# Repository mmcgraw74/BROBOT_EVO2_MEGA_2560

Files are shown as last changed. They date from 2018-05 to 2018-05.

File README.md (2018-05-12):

# BROBOT-EVO2-MEGA-2560

This project is a modification of the JJRobots EVO2 balancing robot:
https://github.com/jjrobots/B-ROBOT_EVO2

I wanted more I/O and program space - so replaced the Arduino Leonardo in the kit with an Arduino Mega 2560.

Since the Mega 2560 is over an inch longer - I used Meshmixer to cut the Stealth files and Simplify3d to stretch and merge the pieces to extend the width of the chassis to 130mm.  My efforts did not get both of the mounting holes in the rear bumper STL - I just drilled a hole manually. 

I had to modify the Leonardo program files for several things that are different in the Mega 2560:
- Mega i2c pins are outside the EVO2 shield - so I plugged two long header pins into the Mega i2c pins and plugged in the i2c CLK and DATA pins from the Gyro cable into the Mega.
- Mega Serial0 (console) is on pins 0 and 1, so I unsoldered the shield pins 0 and 1 out and moved the pins to the top of the board and jumpered the pins to Mega TX1 and RX1.
- I changed the servo code to use the SoftwareServo library. The Servo library conflicted with the Wire library. Then I changed the servo code to make library calls. If I was more proficient at Arduino timer code - I might have been able to not use the softwareservo library and initialize the Mega timers.
- I changed the PORT and bit from Leonardo to Mega 2560 to get the stepper motor code to work with the Mega.
- I merged my Touch OSC code changes which provide battery voltage and battery percentage plus PID values on the PID screen

This is still a work in progress:  the additional mass has not been factored into the default PIDs, so the Mega EVO2 is drivable in PRO mode, but not as stable as the Leonardo EVO2 yet.

All Arduino files are included, my stretched Stealth Remix EVO2 chassis STL files and my TOUCH OSC file - works with my iPHONE6s

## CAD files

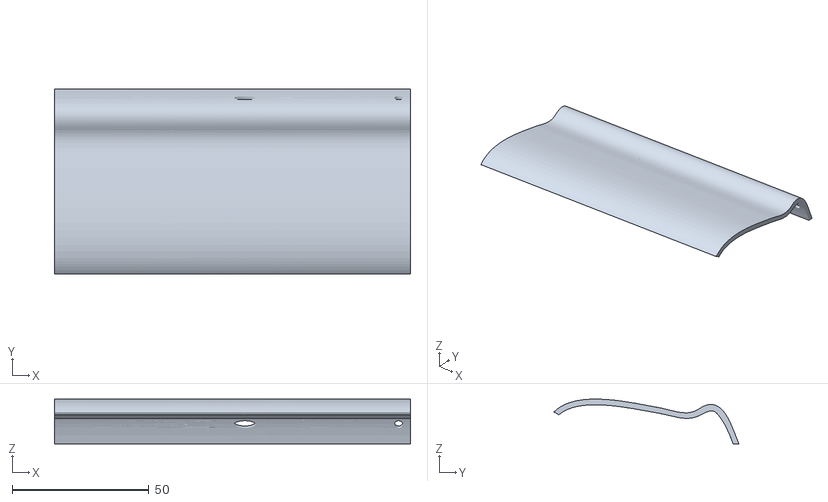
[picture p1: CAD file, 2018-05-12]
EVO2 Mega STL files/130mm front bumper_fixed.stl
130.0 x 67.5 x 16.4

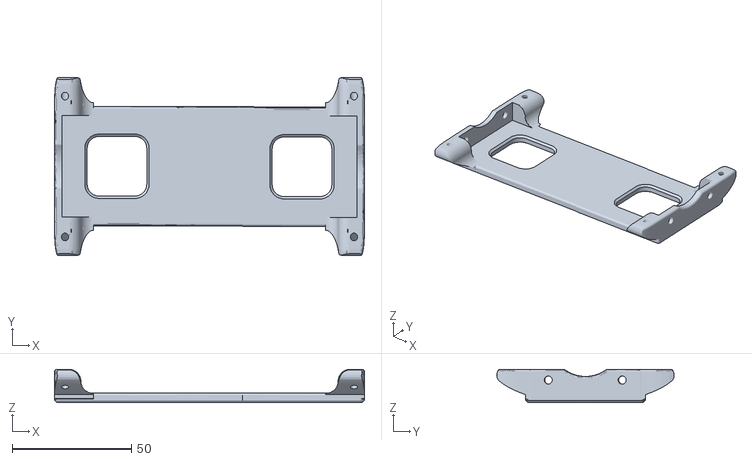
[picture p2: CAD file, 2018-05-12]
EVO2 Mega STL files/130mm motor extended_fixed.stl
130.0 x 74.4 x 14.0

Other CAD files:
EVO2 Mega STL files/130mm back bumper_fixed.stl

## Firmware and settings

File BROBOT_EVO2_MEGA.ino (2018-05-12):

// BROBOT EVO 2 by JJROBOTS
// SELF BALANCE ARDUINO ROBOT WITH STEPPER MOTORS CONTROLLED WITH YOUR SMARTPHONE
// JJROBOTS BROBOT KIT: (Arduino Mega + BROBOT ELECTRONIC BRAIN SHIELD + STEPPER MOTOR drivers)
// This code is prepared for new BROBOT shield  with ESP8266 Wifi module
// Author: JJROBOTS.COM
// Date: 02/09/2014
// Updated: 25/06/2017
// Modified: 10/05/2018 by Monty McGraw (Nikola-wan) for Arduino Mega
// Version: 2.82
// License: GPL v2
// Compiled and tested with Arduino 1.8.5. This modified version of code adds SoftwareServo (only Arduino standard libraries)
// Project URL: http://jjrobots.com/b-robot-evo-2-much-more-than-a-self-balancing-robot (Features,documentation,build instructions,how it works, SHOP,...)
// New updates:
//   - New default parameters specially tuned for BROBOT EVO 2 version (More agile, more stable...)
//   - New Move mode with position control (for externally programming the robot with a Blockly or pyhton programming interfaces)
//   - New telemtry packets send to TELEMETRY IP for monitoring Battery, Angle, ... (old battery packets for touch osc not working now)
//   - Default telemetry server is 192.168.4.2 (first client connected to the robot)
//  Get the free android app (jjrobots) from google play. For IOS users you need to use TouchOSC App + special template (info on jjrobots page)
//  Thanks to our users on the forum for the new ideas. Specially sasa999, KomX, ...

// The board needs at least 10-15 seconds with no motion (robot steady) at beginning to give good values... Robot move slightly when it´s ready!
// MPU6050 IMU connected via I2C bus. Angle estimation using complementary filter (fusion between gyro and accel)
// Angle calculations and control part is running at 100Hz

// The robot is OFF when the angle is high (robot is horizontal). When you start raising the robot it
// automatically switch ON and start a RAISE UP procedure.
// You could RAISE UP the robot also with the robot arm servo (Servo button on the interface)
// To switch OFF the robot you could manually put the robot down on the floor (horizontal)

// We use a standard PID controllers (Proportional, Integral derivative controller) for robot stability
// More info on the project page: How it works page at jjrobots.com
// We have a PI controller for speed control and a PD controller for stability (robot angle)
// The output of the control (motors speed) is integrated so it´s really an acceleration not an speed.

// We control the robot from a WIFI module using OSC standard UDP messages
// You need an OSC app to control de robot (Custom free JJRobots APP for android, and TouchOSC APP for IOS)
// Join the module Wifi Access Point (by default: JJROBOTS_XX) with your Smartphone/Tablet...
//   Wifi password: 87654321
// For TouchOSC users (IOS): Install the BROBOT layout into the OSC app (Touch OSC) and start play! (read the project page)
// OSC controls:
//    fader1: Throttle (0.0-1.0) OSC message: /1/fader1
//    fader2: Steering (0.0-1.0) OSC message: /1/fader2
//    push1: Move servo arm (and robot raiseup) OSC message /1/push1
//    if you enable the touchMessage on TouchOSC options, controls return to center automatically when you lift your fingers
//    PRO mode (PRO button). On PRO mode steering and throttle are more aggressive
//    PAGE2: PID adjustements [optional][dont touch if you dont know what you are doing...;-) ]

#include <Wire.h>
#include <SoftwareServo.h>
SoftwareServo myservo1,myservo2;  // create servo object to control two servos

// Uncomment this lines to connect to an external Wifi router (join an existing Wifi network)
//#define EXTERNAL_WIFI
//#define WIFI_SSID "YOUR_WIFI"
//#define WIFI_PASSWORD "YOUR_PASSWORD"
//#define WIFI_IP "192.168.1.101"  // Force ROBOT IP
//#define TELEMETRY "192.168.1.38" // Tlemetry server port 2223

#define TELEMETRY "192.168.4.2" // Default telemetry server (first client) port 2223

// NORMAL MODE PARAMETERS (MAXIMUN SETTINGS)
#define MAX_THROTTLE 550
#define MAX_STEERING 140
#define MAX_TARGET_ANGLE 14

// PRO MODE = MORE AGGRESSIVE (MAXIMUN SETTINGS)
#define MAX_THROTTLE_PRO 780   // Max recommended value: 860
#define MAX_STEERING_PRO 260   // Max recommended value: 280
#define MAX_TARGET_ANGLE_PRO 26   // Max recommended value: 32

// Default control terms for EVO 2
#define KP 0.32       
#define KD 0.050     
#define KP_THROTTLE 0.080 
#define KI_THROTTLE 0.1

float Kpu_old;
float Kdu_old;
float Kpt_old;
float Kit_old;

#define KP_POSITION 0.06  
#define KD_POSITION 0.45  
//#define KI_POSITION 0.02

// Control gains for raiseup (the raiseup movement requiere special control parameters)
#define KP_RAISEUP 0.1   
#define KD_RAISEUP 0.16   
#define KP_THROTTLE_RAISEUP 0   // No speed control on raiseup
#define KI_THROTTLE_RAISEUP 0.0

#define MAX_CONTROL_OUTPUT 500
#define ITERM_MAX_ERROR 30   // Iterm windup constants for PI control 
#define ITERM_MAX 10000

#define ANGLE_OFFSET 0.0  // Offset angle for balance (to compensate robot own weight distribution)

// Servo definitions
#define SERVO_AUX_NEUTRO 90  // Servo neutral position in degrees
#define SERVO_MIN_PULSEWIDTH 0
#define SERVO_MAX_PULSEWIDTH 180

#define SERVO2_NEUTRO 90
#define SERVO2_RANGE 180


// Telemetry
#define TELEMETRY_BATTERY 1
#define TELEMETRY_ANGLE 1
//#define TELEMETRY_DEBUG 1  // Dont use TELEMETRY_ANGLE and TELEMETRY_DEBUG at the same time!

#define ZERO_SPEED 65535
#define MAX_ACCEL 14      // Maximun motor acceleration (MAX RECOMMENDED VALUE: 20) (default:14)

#define MICROSTEPPING 16   // 8 or 16 for 1/8 or 1/16 driver microstepping (default:16)

#define DEBUG 1   // 0 = No debug info (default) DEBUG 1 for console output

// AUX definitions
#define CLR(x,y) (x&=(~(1<<y)))
#define SET(x,y) (x|=(1<<y))
#define RAD2GRAD 57.2957795
#define GRAD2RAD 0.01745329251994329576923690768489

String MAC;  // MAC address of Wifi module
String tempstring;

unsigned int testVal = 0;
uint8_t cascade_control_loop_counter = 0;
uint8_t loop_counter;       // To generate a medium loop 40Hz
uint8_t slow_loop_counter;  // slow loop 2Hz
uint8_t sendBattery_counter; // To send battery status
int16_t BatteryValue;
static char outstr[4];
float BatteryFloat;
float BatteryReal;

long timer_old;
long timer_value;
float debugVariable;
float dt;

// Angle of the robot (used for stability control)
float angle_adjusted;
float angle_adjusted_Old;
float angle_adjusted_filtered = 0.0;

// Default control values from constant definitions
float Kp = KP;
float Kd = KD;
float Kp_thr = KP_THROTTLE;
float Ki_thr = KI_THROTTLE;
float Kp_user = KP;
float Kd_user = KD;
float Kp_thr_user = KP_THROTTLE;
float Ki_thr_user = KI_THROTTLE;
float Kp_position = KP_POSITION;
float Kd_position = KD_POSITION;
bool newControlParameters = false;
bool modifing_control_parameters = false;
int16_t position_error_sum_M1;
int16_t position_error_sum_M2;
float PID_errorSum;
float PID_errorOld = 0;
float PID_errorOld2 = 0;
float setPointOld = 0;
float target_angle;
int16_t throttle;
float steering;
float max_throttle = MAX_THROTTLE;
float max_steering = MAX_STEERING;
float max_target_angle = MAX_TARGET_ANGLE;
float control_output;
float angle_offset = ANGLE_OFFSET;

boolean positionControlMode = false;
uint8_t mode;  // mode = 0 Normal mode, mode = 1 Pro mode (More agressive)

int16_t motor1;
int16_t motor2;

// position control
volatile int32_t steps1;
volatile int32_t steps2;
int32_t target_steps1;
int32_t target_steps2;
int16_t motor1_control;
int16_t motor2_control;

int16_t speed_M1, speed_M2;        // Actual speed of motors
int8_t  dir_M1, dir_M2;            // Actual direction of steppers motors
int16_t actual_robot_speed;        // overall robot speed (measured from steppers speed)
int16_t actual_robot_speed_Old;
float estimated_speed_filtered;    // Estimated robot speed

// OSC output variables
uint8_t OSCpage;
uint8_t OSCnewMessage;
float OSCfader[4];
float OSCxy1_x;
float OSCxy1_y;
float OSCxy2_x;
float OSCxy2_y;
uint8_t OSCpush[4];
uint8_t OSCtoggle[4];
uint8_t OSCmove_mode;
int16_t OSCmove_speed;
int16_t OSCmove_steps1;
int16_t OSCmove_steps2;


// INITIALIZATION
void setup()
{
  // STEPPER PINS ON JJROBOTS BROBOT BRAIN BOARD
  pinMode(4, OUTPUT); // ENABLE MOTORS
  pinMode(7, OUTPUT); // STEP MOTOR 1 PORTE,6
  pinMode(8, OUTPUT); // DIR MOTOR 1  PORTB,4
  pinMode(12, OUTPUT); // STEP MOTOR 2 PORTD,6
  pinMode(5, OUTPUT); // DIR MOTOR 2  PORTC,6
  digitalWrite(4, HIGH);  // Disable motors
  /*
  pinMode(10, OUTPUT);  // Servo1 (arm)
  pinMode(13, OUTPUT);  // Servo2
  */
  Serial.begin(115200); // Serial output to console
  
  Serial1.begin(115200);
  OSC_init();

  // Initialize I2C bus (MPU6050 is connected via I2C)
  Wire.begin();

#if DEBUG > 0
  delay(9000);
#else
  delay(1000);
#endif
  Serial.println("JJROBOTS");
  delay(200);
  Serial.println("Don't move for 10 sec...");
  MPU6050_setup();  // setup MPU6050 IMU
  delay(500);

  // With the new ESP8266 WIFI MODULE WE NEED TO MAKE AN INITIALIZATION PROCESS
  Serial.println("WIFI init");
  Serial1.flush();
  Serial1.print("+++");  // To ensure we exit the transparent transmision mode
  delay(100);
  ESPsendCommand("AT", "OK", 1);
  ESPsendCommand("AT+RST", "OK", 2); // ESP Wifi module RESET
  ESPwait("ready", 6);
  ESPsendCommand("AT+GMR", "OK", 5);

#ifdef EXTERNAL_WIFI
  ESPsendCommand("AT+CWQAP", "OK", 3);
  ESPsendCommand("AT+CWMODE=1", "OK", 3);
  //String auxCommand = (String)"AT+CWJAP="+WIFI_SSID+","+WIFI_PASSWORD;
  char auxCommand[90] = "AT+CWJAP=\"";
  strcat(auxCommand, WIFI_SSID);
  strcat(auxCommand, "\",\"");
  strcat(auxCommand, WIFI_PASSWORD);
  strcat(auxCommand, "\"");
  ESPsendCommand(auxCommand, "OK", 14);
#ifdef WIFI_IP
  strcpy(auxCommand, "AT+CIPSTA=\"");
  strcat(auxCommand, WIFI_IP);
  strcat(auxCommand, "\"");
  ESPsendCommand(auxCommand, "OK", 4);
#endif
  ESPsendCommand("AT+CIPSTA?", "OK", 4);
#else  // Deafault : we generate a wifi network
  Serial1.println("AT+CIPSTAMAC?");
  ESPgetMac();
  //Serial.print("MAC:");
  //Serial.println(MAC);
  delay(200);
  ESPsendCommand("AT+CWQAP", "OK", 3);
  ESPsendCommand("AT+CWMODE=2", "OK", 3); // Soft AP mode
  // Generate Soft AP. SSID=JJROBOTS, PASS=87654321
  char *cmd =  "AT+CWSAP=\"JJROBOTS_XX\",\"87654321\",5,3";
  // Update XX characters with MAC address (last 2 characters)
  cmd[19] = MAC[10];
  cmd[20] = MAC[11];
  ESPsendCommand(cmd, "OK", 6);
#endif
  // Start UDP SERVER on port 2222, telemetry port 2223
  Serial.println("Start UDP server");
  ESPsendCommand("AT+CIPMUX=0", "OK", 3);  // Single connection mode
  ESPsendCommand("AT+CIPMODE=1", "OK", 3); // Transparent mode
  char Telemetry[80];
  strcpy(Telemetry, "AT+CIPSTART=\"UDP\",\"");
  strcat(Telemetry, TELEMETRY);
  strcat(Telemetry, "\",2223,2222,0");
  ESPsendCommand(Telemetry, "OK", 3); 

  // Calibrate gyros
  MPU6050_calibrate();

  ESPsendCommand("AT+CIPSEND", ">", 2); // Start transmission (transparent mode)

  // Init servos
  Serial.println("Servo init");
  BROBOT_initServo();

  myservo1.attach(10);
  myservo2.attach(13);
  myservo1.write(SERVO_AUX_NEUTRO);
  myservo2.write(SERVO_AUX_NEUTRO);
  SoftwareServo::refresh();

  // STEPPER MOTORS INITIALIZATION
  Serial.println("Steppers init");
  //MOTOR1 => TIMER1
  TCCR1A = 0;                       // Timer1 CTC mode 4, OCxA,B outputs disconnected
  TCCR1B = (1 << WGM12) | (1 << CS11); // Prescaler=8, => 2Mhz
  OCR1A = ZERO_SPEED;               // Motor stopped
  dir_M1 = 0;
  TCNT1 = 0;

  // MOTOR2 => TIMER3
  TCCR3A = 0;                       // Timer3 CTC mode 4, OCxA,B outputs disconnected
  TCCR3B = (1 << WGM32) | (1 << CS31); // Prescaler=8, => 2Mhz
  OCR3A = ZERO_SPEED;   // Motor stopped
  dir_M2 = 0;
  TCNT3 = 0;
  delay(200);

  // Enable stepper drivers and TIMER interrupts
  digitalWrite(4, LOW);   // Enable stepper drivers
  // Enable TIMERs interrupts
  TIMSK1 |= (1 << OCIE1A); // Enable Timer1 interrupt
  TIMSK3 |= (1 << OCIE1A); // Enable Timer1 interrupt
  
  
  // Little motor vibration and servo move to indicate that robot is ready
  for (uint8_t k = 0; k < 5; k++)
  {
    /*setMotorSpeedM1(5);
    setMotorSpeedM2(5);
    */
    myservo1.write(SERVO_AUX_NEUTRO + 10);
    myservo2.write(SERVO2_NEUTRO + 10);
    SoftwareServo::refresh();
    delay(200);
    /* setMotorSpeedM1(-5);
    setMotorSpeedM2(-5);
    */
    
    myservo1.write(SERVO_AUX_NEUTRO - 10);
    myservo2.write(SERVO2_NEUTRO - 10);
    SoftwareServo::refresh();
    delay(200);
  }
  myservo1.write(SERVO_AUX_NEUTRO);
  myservo2.write(SERVO2_NEUTRO);
  SoftwareServo::refresh();

 #if TELEMETRY_BATTERY==1
  BatteryValue = BROBOT_readBattery(true);
  Serial.print("BATT:");
  Serial.println(BatteryValue);
#endif
  Serial.println("BROBOT by JJROBOTS v2.82");
  Serial.println("Start...");
  timer_old = micros();
}


// MAIN LOOP
void loop()
{
  OSC_MsgRead();  // Read UDP OSC messages
  if (OSCnewMessage)
  {
    OSCnewMessage = 0;
    if (OSCpage == 1)   // Get commands from user (PAGE1 are user commands: throttle, steering...)
    {
      if (modifing_control_parameters)  // We came from the settings screen
      {
        OSCfader[0] = 0.5; // default neutral values
        OSCfader[1] = 0.5;
        OSCtoggle[0] = 0;  // Normal mode
        mode = 0;
        modifing_control_parameters = false;
      }

      if (OSCmove_mode)
      {
        //Serial.print("M ");
        //Serial.print(OSCmove_speed);
        //Serial.print(" ");
        //Serial.print(OSCmove_steps1);
        //Serial.print(",");
        //Serial.println(OSCmove_steps2);
        positionControlMode = true;
        OSCmove_mode = false;
        target_steps1 = steps1 + OSCmove_steps1;
        target_steps2 = steps2 + OSCmove_steps2;
      }
      else
      {
        positionControlMode = false;
        throttle = (OSCfader[0] - 0.5) * max_throttle;
        // We add some exponential on steering to smooth the center band
        steering = OSCfader[1] - 0.5;
        if (steering > 0)
          steering = (steering * steering + 0.5 * steering) * max_steering;
        else
          steering = (-steering * steering + 0.5 * steering) * max_steering;
      }

      if ((mode == 0) && (OSCtoggle[0]))
      {
        // Change to PRO mode
        max_throttle = MAX_THROTTLE_PRO;
        max_steering = MAX_STEERING_PRO;
        max_target_angle = MAX_TARGET_ANGLE_PRO;
        mode = 1;
      }
      if ((mode == 1) && (OSCtoggle[0] == 0))
      {
        // Change to NORMAL mode
        max_throttle = MAX_THROTTLE;
        max_steering = MAX_STEERING;
        max_target_angle = MAX_TARGET_ANGLE;
        mode = 0;
      }
    }
    else if (OSCpage == 2) { // OSC page 2
      // Check for new user control parameters
      readControlParameters();
    }
#if DEBUG==1
    Serial.print(throttle);
    Serial.print(" ");
    Serial.println(steering);
#endif
  } // End new OSC message

  timer_value = micros();

  // New IMU data?
  if (MPU6050_newData())
  {
    MPU6050_read_3axis();
    loop_counter++;
    slow_loop_counter++;
    dt = (timer_value - timer_old) * 0.000001; // dt in seconds
    timer_old = timer_value;

    angle_adjusted_Old = angle_adjusted;
    // Get new orientation angle from IMU (MPU6050)
    float MPU_sensor_angle = MPU6050_getAngle(dt);
    angle_adjusted = MPU_sensor_angle + angle_offset;
    if ((MPU_sensor_angle>-15)&&(MPU_sensor_angle<15))
      angle_adjusted_filtered = angle_adjusted_filtered*0.99 + MPU_sensor_angle*0.01;
      
#if DEBUG==1
    Serial.print(dt);
    Serial.print(" ");
    Serial.print(angle_offset);
    Serial.print(" ");
    Serial.print(angle_adjusted);
    Serial.print(",");
    Serial.println(angle_adjusted_filtered);
#endif
    //Serial.print("\t");

    // We calculate the estimated robot speed:
    // Estimated_Speed = angular_velocity_of_stepper_motors(combined) - angular_velocity_of_robot(angle measured by IMU)
    actual_robot_speed = (speed_M1 + speed_M2) / 2; // Positive: forward  

    int16_t angular_velocity = (angle_adjusted - angle_adjusted_Old) * 25.0; // 25 is an empirical extracted factor to adjust for real units
    int16_t estimated_speed = -actual_robot_speed + angular_velocity;
    estimated_speed_filtered = estimated_speed_filtered * 0.9 + (float)estimated_speed * 0.1; // low pass filter on estimated speed

#if DEBUG==2
    Serial.print(angle_adjusted);
    Serial.print(" ");
    Serial.println(estimated_speed_filtered);
#endif

    if (positionControlMode)
    {
      // POSITION CONTROL. INPUT: Target steps for each motor. Output: motors speed
      motor1_control = positionPDControl(steps1, target_steps1, Kp_position, Kd_position, speed_M1);
      motor2_control = positionPDControl(steps2, target_steps2, Kp_position, Kd_position, speed_M2);

      // Convert from motor position control to throttle / steering commands
      throttle = (motor1_control + motor2_control) / 2;
      throttle = constrain(throttle, -190, 190);
      steering = motor2_control - motor1_control;
      steering = constrain(steering, -50, 50);
    }

    // ROBOT SPEED CONTROL: This is a PI controller.
    //    input:user throttle(robot speed), variable: estimated robot speed, output: target robot angle to get the desired speed
    target_angle = speedPIControl(dt, estimated_speed_filtered, throttle, Kp_thr, Ki_thr);
    target_angle = constrain(target_angle, -max_target_angle, max_target_angle); // limited output
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

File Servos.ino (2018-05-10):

// BROBOT EVO 2 by JJROBOTS
// SELF BALANCE ARDUINO ROBOT WITH STEPPER MOTORS
// License: GPL v2
// Servo and aux functions

//#include "Arduino.h"

/* Default servo definitions  commented out by MCM - we are using Servo library
#define SERVO1_AUX_NEUTRO 1500  // Servo neutral position
#define SERVO1_MIN_PULSEWIDTH 700
#define SERVO1_MAX_PULSEWIDTH 2300
#define SERVO2_AUX_NEUTRO 1500  // Servo neutral position
#define SERVO2_MIN_PULSEWIDTH 700
#define SERVO2_MAX_PULSEWIDTH 2300
*/

#define BATT_VOLT_FACTOR 8

int battery;

// Init servo on T4 timer. Output OC4B (Leonardo Pin10)
// We configure the Timer4 for 11 bits PWM (enhacend precision) and 16.3ms period (OK for most servos)
// Resolution: 8us per step (this is OK for servos, around 175 steps for typical servo)

/*
void BROBOT_initServo()
{
int temp;

  // Initialize Timer4 as Fast PWM
  TCCR4A = (1<<PWM4A)|(1<<PWM4B);
  TCCR4B = 0;
  TCCR4C = (1<<PWM4D);
  TCCR4D = 0;
  TCCR4E = (1<<ENHC4); // Enhanced -> 11 bits

  temp = 1500>>3;
  TC4H = temp >> 8;
  OCR4B = temp & 0xff;

  // Reset timer
  TC4H = 0;
  TCNT4 = 0;

  // Set TOP to 1023 (10 bit timer)
  TC4H = 3;
  OCR4C = 0xFF;

  // OC4A = PC7 (Pin13)  OC4B = PB6 (Pin10)   OC4D = PD7 (Pin6)
  // Set pins as outputs
  DDRB |= (1 << 6);  // OC4B = PB6 (Pin10 on Leonardo board)
  DDRC |= (1 << 7);  // OC4A = PC7 (Pin13 on Leonardo board)
  DDRD |= (1 << 7);  // OC4D = PD7 (Pin6 on Leonardo board)

  //Enable OC4A and OC4B and OCR4D output
  TCCR4A |= (1<<COM4B1)|(1<<COM4A1); 
  TCCR4C |= (1<<COM4D1);
  // set prescaler to 256 and enable timer    16Mhz/256/1024 = 61Hz (16.3ms)
  TCCR4B = (1 << CS43)|(1 << CS40);
}

void BROBOT_moveServo1(int pwm)
{
  pwm = constrain(pwm,SERVO1_MIN_PULSEWIDTH,SERVO1_MAX_PULSEWIDTH)>>3;  // Check max values and Resolution: 8us
  // 11 bits => 3 MSB bits on TC4H, LSB bits on OCR4B
  TC4H = pwm>>8;
  OCR4B = pwm & 0xFF;
}

void BROBOT_moveServo2(int pwm)
{
  pwm = constrain(pwm,SERVO2_MIN_PULSEWIDTH,SERVO2_MAX_PULSEWIDTH)>>3;  // Check max values and Resolution: 8us
  // 11 bits => 3 MSB bits on TC4H, LSB bits on OCR4B
  TC4H = pwm>>8;
  OCR4A = pwm & 0xFF;  // 2.0 or 2.3  boards servo2 output
  OCR4D = pwm & 0xFF;  // 2.1 or 2.4  boards servo2 output
}
*/

// output : Battery voltage*10 (aprox) and noise filtered
int BROBOT_readBattery(bool first_time)
{
  if (first_time)
	battery = analogRead(5)/BATT_VOLT_FACTOR;
  else
    battery = (battery*9 + (analogRead(5)/BATT_VOLT_FACTOR))/10;
  return battery;
}

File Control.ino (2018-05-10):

// BROBOT EVO 2 by JJROBOTS
// SELF BALANCE ARDUINO ROBOT WITH STEPPER MOTORS
// License: GPL v2
// Control functions (PID controls, Steppers control...)

// PD controller implementation(Proportional, derivative). DT in seconds
float stabilityPDControl(float DT, float input, float setPoint,  float Kp, float Kd)
{
  float error;
  float output;

  error = setPoint - input;

  // Kd is implemented in two parts
  //    The biggest one using only the input (sensor) part not the SetPoint input-input(t-1).
  //    And the second using the setpoint to make it a bit more agressive   setPoint-setPoint(t-1)
  float Kd_setPoint = constrain((setPoint - setPointOld), -8, 8); // We limit the input part...
  output = Kp * error + (Kd * Kd_setPoint - Kd * (input - PID_errorOld)) / DT;
  //Serial.print(Kd*(error-PID_errorOld));Serial.print("\t");
  //PID_errorOld2 = PID_errorOld;
  PID_errorOld = input;  // error for Kd is only the input component
  setPointOld = setPoint;
  return (output);
}


// PI controller implementation (Proportional, integral). DT in seconds
float speedPIControl(float DT, int16_t input, int16_t setPoint,  float Kp, float Ki)
{
  int16_t error;
  float output;

  error = setPoint - input;
  PID_errorSum += constrain(error, -ITERM_MAX_ERROR, ITERM_MAX_ERROR);
  PID_errorSum = constrain(PID_errorSum, -ITERM_MAX, ITERM_MAX);

  //Serial.println(PID_errorSum);

  output = Kp * error + Ki * PID_errorSum * DT; // DT is in miliseconds...
  return (output);
}


float positionPDControl(long actualPos, long setPointPos, float Kpp, float Kdp, int16_t speedM)
{
  float output;
  float P;

  P = constrain(Kpp * float(setPointPos - actualPos), -115, 115); // Limit command
  output = P + Kdp * float(speedM);
  return (output);
}

// TIMER 1 : STEPPER MOTOR1 SPEED CONTROL
ISR(TIMER1_COMPA_vect)
{
  if (dir_M1 == 0) // If we are not moving we dont generate a pulse
    return;
  // We generate 1us STEP pulse
  SET(PORTH, 4); // STEP MOTOR 1
  //delay_1us();
  if (dir_M1 > 0)
    steps1--;
  else
    steps1++;
  CLR(PORTH, 4);
}
// TIMER 3 : STEPPER MOTOR2 SPEED CONTROL
ISR(TIMER3_COMPA_vect)
{
  if (dir_M2 == 0) // If we are not moving we dont generate a pulse
    return;
  // We generate 1us STEP pulse
  SET(PORTB, 6); // STEP MOTOR 2
  //delay_1us();
  if (dir_M2 > 0)
    steps2--;
  else
    steps2++;
  CLR(PORTB, 6);
}


// Set speed of Stepper Motor1
// tspeed could be positive or negative (reverse)
void setMotorSpeedM1(int16_t tspeed)
{
  long timer_period;
  int16_t speed;

  // Limit max speed?

  // WE LIMIT MAX ACCELERATION of the motors
  if ((speed_M1 - tspeed) > MAX_ACCEL)
    speed_M1 -= MAX_ACCEL;
  else if ((speed_M1 - tspeed) < -MAX_ACCEL)
    speed_M1 += MAX_ACCEL;
  else
    speed_M1 = tspeed;

#if MICROSTEPPING==16
  speed = speed_M1 * 50; // Adjust factor from control output speed to real motor speed in steps/second
#else
  speed = speed_M1 * 25; // 1/8 Microstepping
#endif

  if (speed == 0)
  {
    timer_period = ZERO_SPEED;
    dir_M1 = 0;
  }
  else if (speed > 0)
  {
    timer_period = 2000000 / speed; // 2Mhz timer
    dir_M1 = 1;
    SET(PORTH, 5); // DIR Motor 1 (Forward)
  }
  else
  {
    timer_period = 2000000 / -speed;
    dir_M1 = -1;
    CLR(PORTH, 5); // Dir Motor 1
  }
  if (timer_period > 65535)   // Check for minimun speed (maximun period without overflow)
    timer_period = ZERO_SPEED;

  OCR1A = timer_period;
  // Check  if we need to reset the timer...
  if (TCNT1 > OCR1A)
    TCNT1 = 0;
}

// Set speed of Stepper Motor2
// tspeed could be positive or negative (reverse)
void setMotorSpeedM2(int16_t tspeed)
{
  long timer_period;
  int16_t speed;

  // Limit max speed?

  // WE LIMIT MAX ACCELERATION of the motors
  if ((speed_M2 - tspeed) > MAX_ACCEL)
    speed_M2 -= MAX_ACCEL;
  else if ((speed_M2 - tspeed) < -MAX_ACCEL)
    speed_M2 += MAX_ACCEL;
  else
    speed_M2 = tspeed;

#if MICROSTEPPING==16
  speed = speed_M2 * 50; // Adjust factor from control output speed to real motor speed in steps/second
#else
  speed = speed_M2 * 25; // 1/8 Microstepping
#endif

  if (speed == 0)
  {
    timer_period = ZERO_SPEED;
    dir_M2 = 0;
  }
  else if (speed > 0)
  {
    timer_period = 2000000 / speed; // 2Mhz timer
    dir_M2 = 1;
    CLR(PORTE, 3);   // Dir Motor2 (Forward)
  }
  else
  {
    timer_period = 2000000 / -speed;
    dir_M2 = -1;
    SET(PORTE, 3);  // DIR Motor 2
  }
  if (timer_period > 65535)   // Check for minimun speed (maximun period without overflow)
    timer_period = ZERO_SPEED;

  OCR3A = timer_period;
  // Check  if we need to reset the timer...
  if (TCNT3 > OCR3A)
    TCNT3 = 0;
}

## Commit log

2018-05-12 Updated for battery voltages
2018-05-12 EVO2 Stealth Mega STL files
    [130mm back bumper_fixed.stl, 130mm front bumper_fixed.stl, 130mm motor extended_fixed.stl]
